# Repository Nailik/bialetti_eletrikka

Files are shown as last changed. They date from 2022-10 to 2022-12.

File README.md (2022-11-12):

# Bialetti Eletrikka

Modifiaction of the Bialetti Eletrikka in order to control the Heat by a Microcontroller with multiple TSiC Temperatur Sensors.

Currently the PCB is created and some sample/test software in development.

Preview of the PCB inside the Bottom of the Machine (the Bottom neeeds to be custom 3d printed).

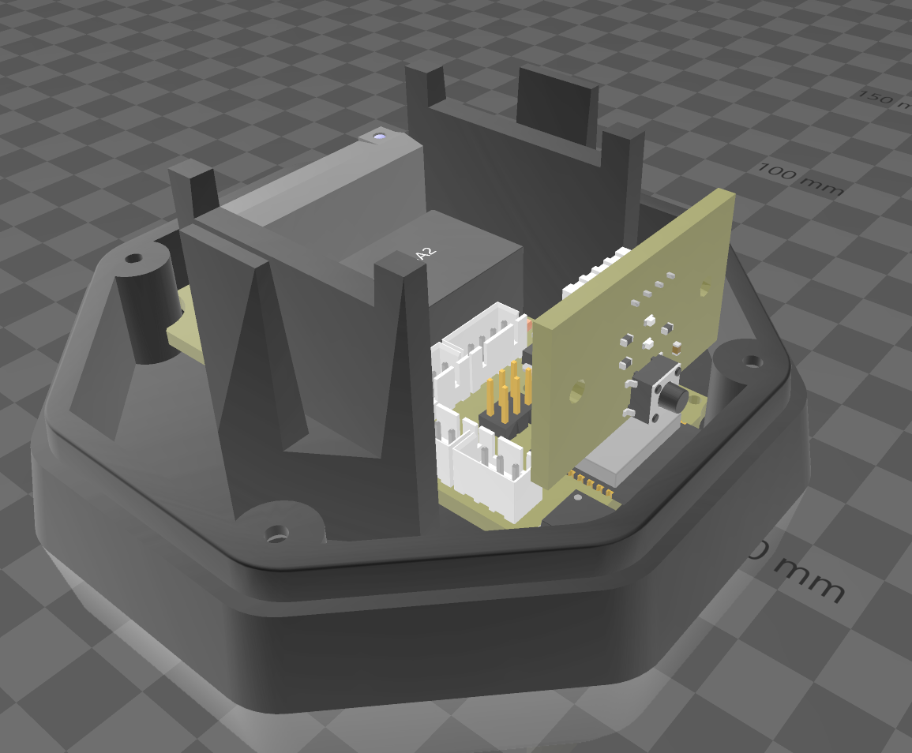
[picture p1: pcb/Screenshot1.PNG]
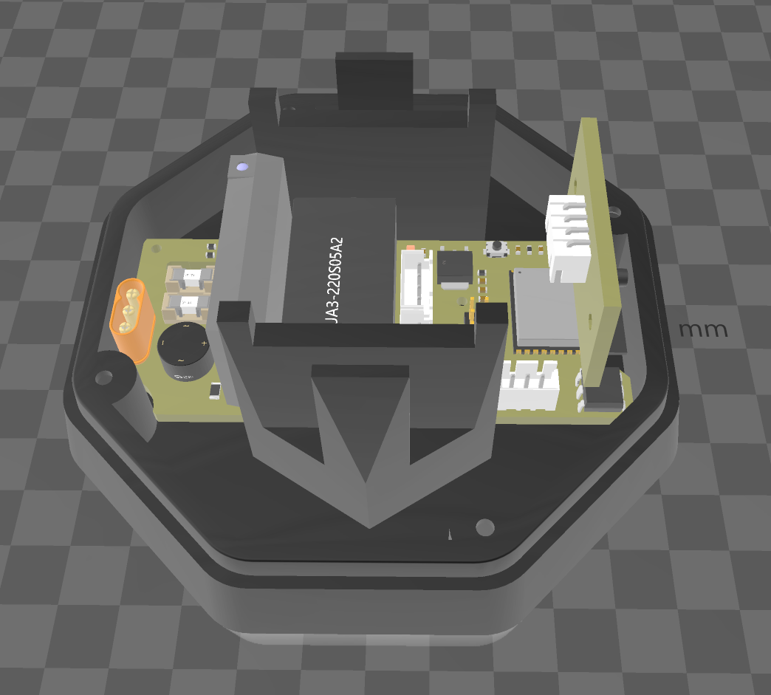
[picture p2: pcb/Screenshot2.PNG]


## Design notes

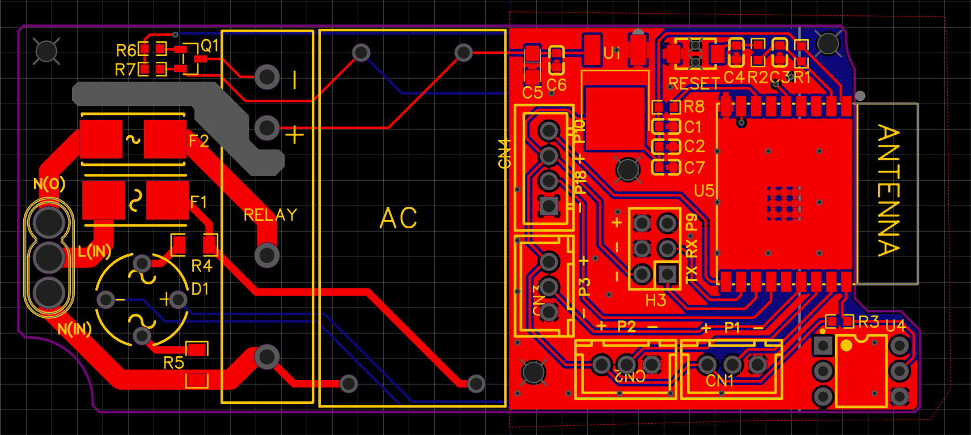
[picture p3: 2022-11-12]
pcb/Electric Mokka Pot-SSR/PCB.PNG

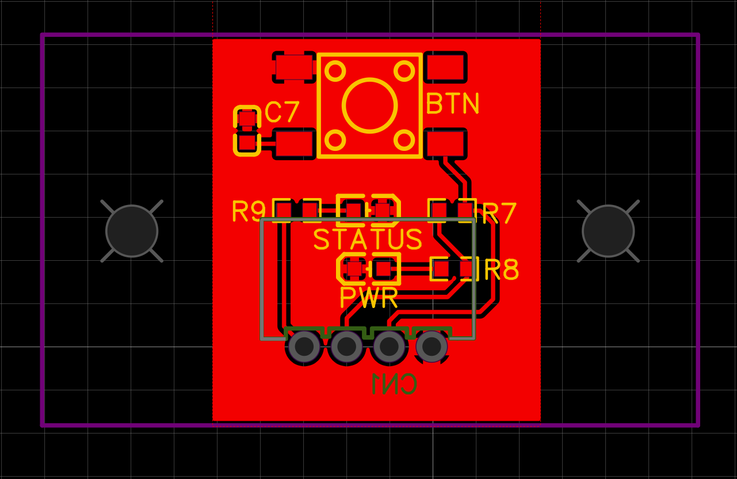
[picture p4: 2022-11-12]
pcb/Electric Mokka Pot - Button/PCB.PNG

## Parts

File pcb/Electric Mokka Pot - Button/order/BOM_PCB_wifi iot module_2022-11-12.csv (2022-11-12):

ID | Name | Designator | Footprint | Quantity | Manufacturer Part | Manufacturer | Supplier | Supplier Part | Price
1 | 0.1uf | C7 | C0603 | 1
2 | 10k | R7 | R0603 | 1
3 | UK-B0228-G5-160-JZ | BTN | KEY-SMD_4P-L6.0-W6.0-P4.50-LS11.0 | 1 | UK-B0228-G5-160-JZ | USAKRO | LCSC
4 | 68Ω | R8 | R0603 | 1
5 | 15Ω | R9 | R0603 | 1
6 | C2290 | PWR,STATUS | LED0603-R-RD_WHITE | 2 | 0603White light | KENTO | LCSC
7 | XH2.54-4AW | CN1 | CONN-TH_XH2.54-4AW | 1 | XH2.54-4AW | BOOMELE | LCSC

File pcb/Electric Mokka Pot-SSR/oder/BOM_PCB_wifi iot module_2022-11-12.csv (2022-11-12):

ID | Name | Designator | Footprint | Quantity | Manufacturer Part | Manufacturer | Supplier | Supplier Part | Price
1 | XH-4A | CN4 | CONN-TH_4P-P2.50_XH-4A | 1 | XH-4A | BOOMELE | LCSC
2 | XH-3A | CN1,CN2,CN3 | CONN-TH_XH-3A | 3 | XH-3A | BOOMELE | LCSC
3 | ESP32-C3-WROOM-02-N4(4MB) | U5 | BULETM-SMD_ESPRESSIF_ESP32-C3-WROOM-02-N4-4MB | 1 | ESP32-C3-WROOM-02-N4(4MB) | ESPRESSIF 乐鑫 | LCSC
4 | 10k | R8,R1,R3 | R0603 | 3
5 | PZ254V-12-6P | H3 | HDR-TH_6P-P2.54-V-M-R2-C3-S2.54 | 1 | PZ254V-12-6P | XFCN | LCSC
6 | 10uf | C1,C7 | C0603 | 2
7 | 0.1uf | C2,C4,C6 | C0603 | 3
8 | 1uf | C3 | C0603 | 1
9 | 0 | R2 | R0603 | 1
10 | 2K2 | R6 | R0603 | 1
11 | 10K | R7 | R0603 | 1
12 | 2N7002 | Q1 | SOT-23-3_L2.9-W1.3-P1.90-LS2.4-BR | 1 | 2N7002 | CJ | LCSC
13 | MR30-M | U2 | CONN-TH_MR30-M | 1 | MR30-M | AMASS(艾迈斯) | LCSC
14 | UA3-220S05A2 | PWR | PWRM-TH_UA3-220S05A2 | 1 | UA3-220S05A2 | Guangzhou Aipu Elec Tech | LCSC
15 | KSD203AC2 | RELAY | OPTO-TH_KSD203AC2 | 1 | KSD203AC2 | cosmo(冠西) | LCSC
16 | LD1117DT33TR | U1 | TO-252-2_L6.6-W6.1-P4.57-LS9.9-BR-CW | 1 | LD1117DT33TR | STMicroelectronics | LCSC
17 | 2W10M | D1 | DIO-BG-TH_WOB | 1 | 2W10M | Semtech | LCSC
18 | CT4N25 | U4 | DIP-6_L7.1-W6.5-P2.54-LS7.6-BL | 1 | CT4N25 | CT Micro International | LCSC
19 | TS-1088-AC02516 | RESET | SW-SMD_L4.0-W2.9-LS4.8 | 1 | TS-1088-AC02516 | XUNPU | LCSC
20 | 30kΩ | R4,R5 | R1206 | 2 | 1206W4F3002T5E | UNI-ROYAL(厚声) | LCSC
21 | 47uf | C5 | CASE-A_3216 | 1
22 | 0154002.DR | F1 | FUSE-SMD_L9.7-W5.0-1 | 1 | 0154002.DR | Littelfuse(美国力特) | LCSC
23 | 0154003.DR | F2 | FUSE-SMD_L9.7-W5.0 | 1 | 0154003.DR | Littelfuse | LCSC

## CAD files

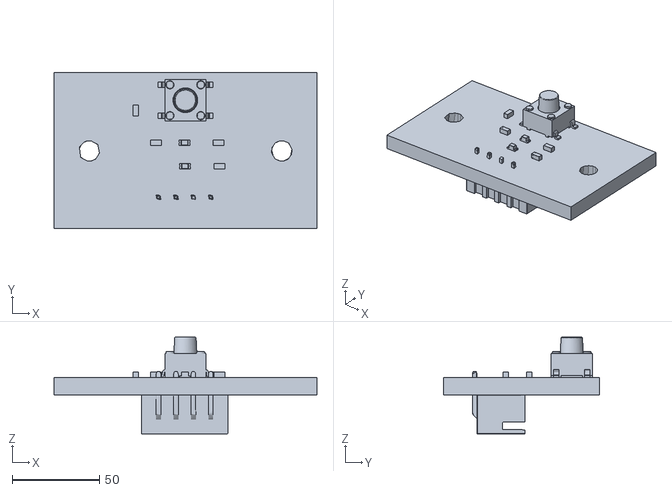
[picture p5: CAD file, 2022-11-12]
pcb/3d/Button/OBJ_PCB_wifi iot module.obj
150.8 x 89.3 x 55.5

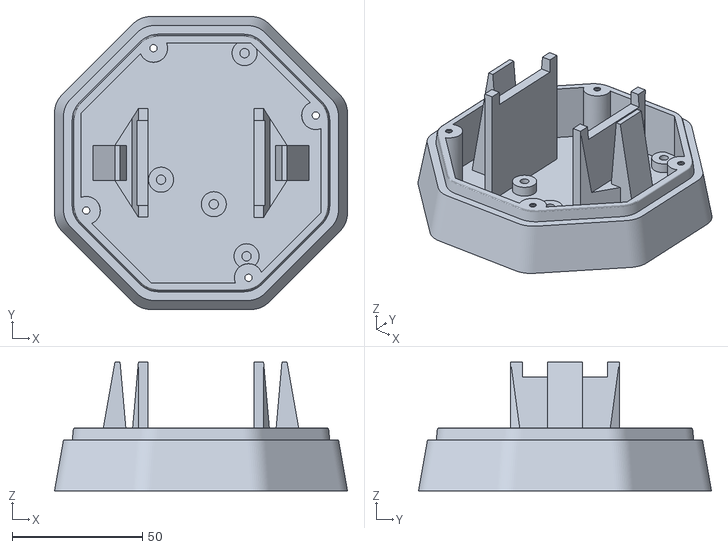
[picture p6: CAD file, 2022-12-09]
pcb/3d/Case.stl
112.3 x 112.3 x 49.3

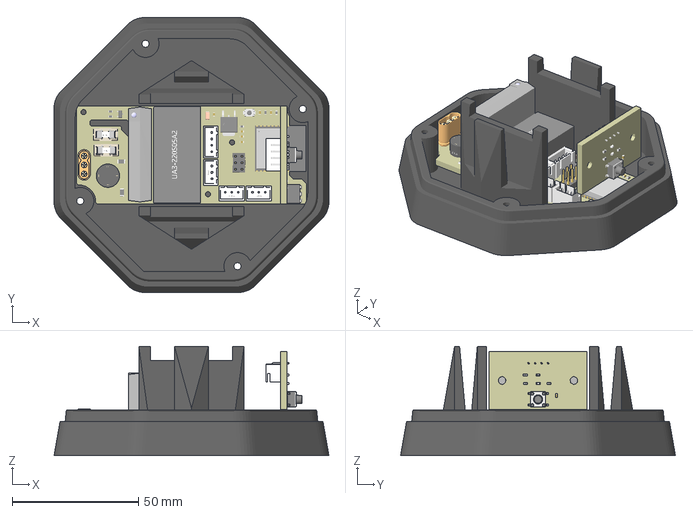
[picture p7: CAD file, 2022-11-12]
pcb/3d/fitcheck.3mf
108.8 x 108.8 x 43.3 mm

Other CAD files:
pcb/3d/mokka bottom v33.f3d

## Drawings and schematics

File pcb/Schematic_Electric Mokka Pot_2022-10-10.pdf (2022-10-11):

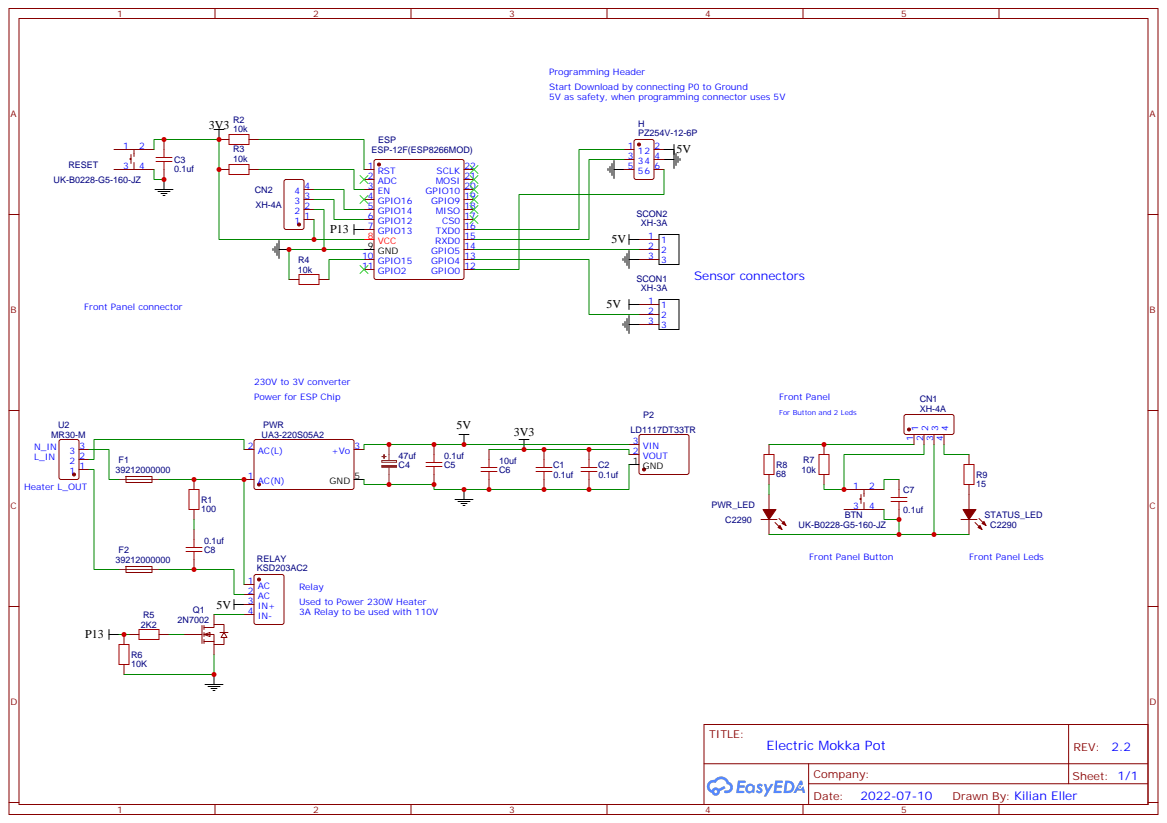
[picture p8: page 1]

Programming Header
Start Download by connecting P0 to Ground
5V as safety, when programming connector uses 5V

230V to 3V converter
Power for ESP Chip

For Button and 2 Leds

Relay
Used to Power 230W Heater
3A Relay to be used with 110V

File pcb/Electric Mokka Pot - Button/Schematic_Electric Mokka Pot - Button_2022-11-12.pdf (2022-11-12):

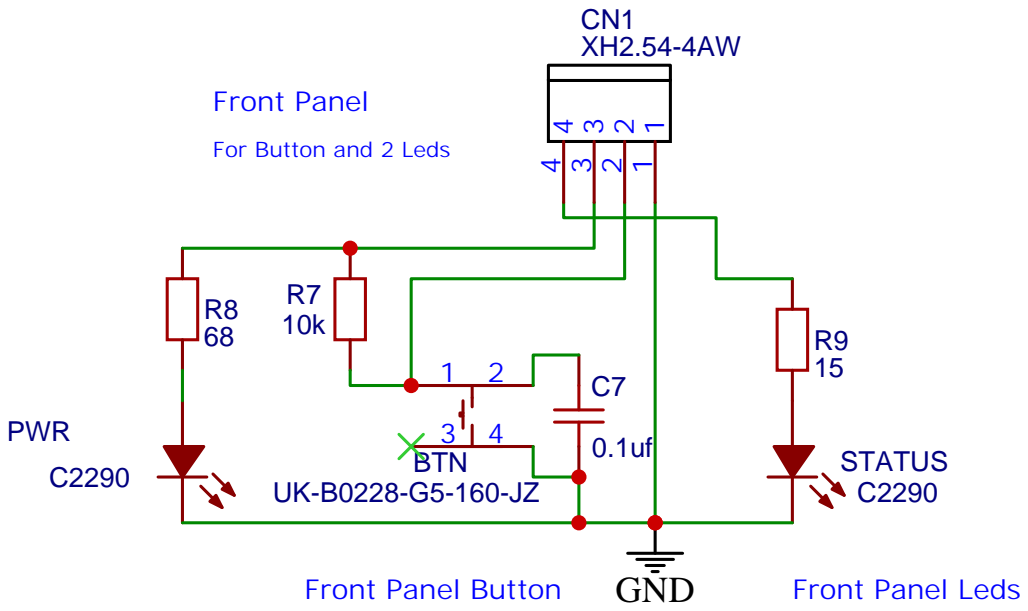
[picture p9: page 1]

For Button and 2 Leds

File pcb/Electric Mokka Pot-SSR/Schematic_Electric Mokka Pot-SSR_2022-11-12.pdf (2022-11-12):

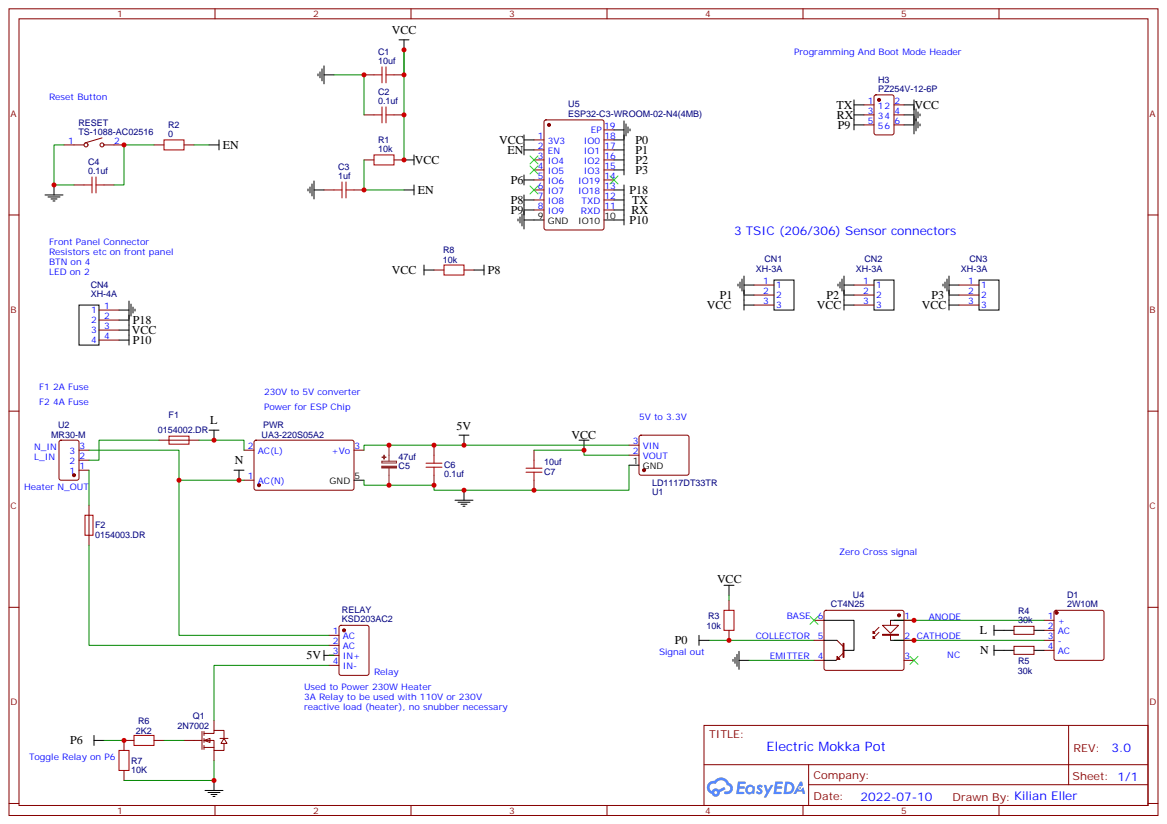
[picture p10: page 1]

Programming And Boot Mode Header

Front Panel Connector
Resistors etc on front panel
BTN on 4
LED on 2

Used to Power 230W Heater
3A Relay to be used with 110V or 230V
reactive load (heater), no snubber necessary

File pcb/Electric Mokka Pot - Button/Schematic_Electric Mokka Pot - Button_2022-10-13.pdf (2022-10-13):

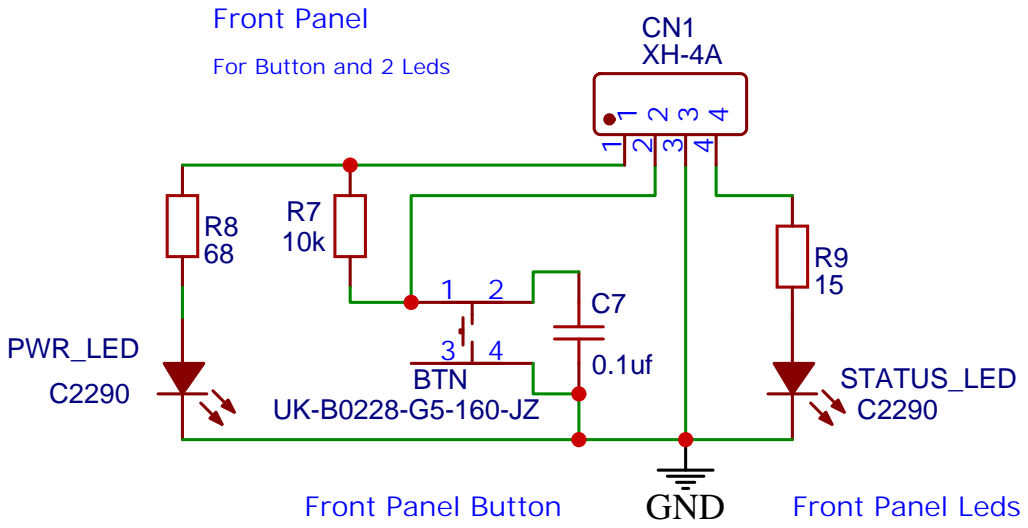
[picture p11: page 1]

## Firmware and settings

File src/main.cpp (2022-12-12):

#include <Arduino.h>
#include "webserver.h"
#include "sensors.h"
#include "actions.h"
#include "pid.h"
#include "WebSerialLite.h"

//https://github.com/Dlloydev/QuickPID
//https://github.com/Dlloydev/sTune
void setup() {
    Serial.begin(115200);
    Serial.println("startup");
    // put your setup code here, to run once:
    Sensors::setup();
    Serial.println("Sensors");
    Actions::setup();
    Serial.println("Actions");
    WebServer::setup();
    Serial.println("WebServer ");
    Pid::setup();
}

void loop() {
    // put your main code here, to run repeatedly:
    Sensors::loop();
    //custom loop for pid
    WebServer::loop();

    if (Serial.available()) {      // If anything comes in Serial (USB),
        WebSerial.println(Serial.readString());
    }

    delay(100);
}

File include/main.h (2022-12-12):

//
// Created by kilia on 12.08.2022.
//

#ifndef UNTITLED_MAIN_H
#define UNTITLED_MAIN_H

#define PIN_LED 10     //status led
#define PIN_BUTTON 18  //button
#define PIN_RELAY 6 //relay on/off
#define PIN_SENSOR_1 1 //TsiC 1
#define PIN_SENSOR_2 2 //TsiC 2
#define PIN_SENSOR_3 3 //TsiC 3 - connected initial
#define PIN_SIGNAL_ZC 0 //zero cross signal

#endif //UNTITLED_MAIN_H

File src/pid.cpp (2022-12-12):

/******************************************************************
  sTune QuickPID Example
  This sketch does on-the-fly tunning and PID Digital Output control
  of a thermal heater (TIP31C). Tunning parameters are quickly
  determined and applied during the temperature ramp-up to setpoint.
  Open the serial plotter to view the graphical results.

bei 65 grad kocht das wasser schon

 ----------------------------------------------
 testTimeSec = 50
 SetPoint = 40
 outputStep = 1

  .00
 Sampl:        0.1000

 Pv Start:          0.000
 Pv Max:            50.418
 Pv Diff:           50.418

 Process Gain:      252.092
 Dead Time Sec:     1.209
 Tau Sec:           87.079

 Tau/Dead Time:     72.0 (easy to control)
 Tau/Sample Period: 870.8 (good sample rate)

 Tuning Method: NoOvershoot_PID
  Kp: 0.171
  Ki: 0.011  Ti: 14.926
  Kd: 1.654  Td: 0.104


   ----------------------------------------------
 SetPoint = 65 (overshoot in beginning big, later up to 67,5°C)
 outputStep = 10
 directIP

  Ip Pv:             34.250
 Pv Start:          0.000
 Pv Max:            162.689
 Pv Diff:           162.689

 Process Gain:      271.148
 Dead Time Sec:     1.207
 Tau Sec:           1.880

 Tau/Dead Time:     1.6 (easy to control)
 Tau/Sample Period: 56.4 (good sample rate)

 Tuning Method: NoOvershoot_PID
  Kp: 0.003
  Ki: 0.532  Ti: 0.006
  Kd: 1.658  Td: 0.002





 ________________________________________





 Testen:


 Heizen -> Druckaufbau -> mehr Energie notwendig
 sobald Druck > Kaffee Druck -> Druck fällt -> weniger Energie notwendig
 Wasser neigt sich Ende -> deutlich weniger Energie -> zufuhr Abschalten, kein Sprudeln

 eigenes soft pwm
 tau (differenz zwischen windows messen bei x energie)
 0 - 100% energie





  *****************************************************************/

#include <cstdint>
#include "sensors.h"
#include "pid.h"
#include "main.h"
#include <Arduino.h>

float Pid::Output = 480;
float Pid::SetPoint = 98;
float Pid::FirstSetPoint = 80;
float Pid::Offset = 1;
float Pid::MaximumOutput = 480;
//window size in ms
uint32_t Pid::WindowSize = 480;
float Pid::TempLimit = 120;
int Pid::ZCTime = 0;
unsigned long Pid::ZCTimeLast = 0;
int Pid::value = 0;

void Pid::setup() {
    pinMode(PIN_RELAY, OUTPUT);
    digitalWrite(PIN_RELAY, LOW);

    attachInterrupt(digitalPinToInterrupt(PIN_SIGNAL_ZC), read, RISING);
}

//läuft alle 100 ms
void Pid::loop() {
    //Pid::zero_cross_int();
}

//output = ms zeit im fenster
float Pid::softPwm(float input, float output, float setpoint, uint32_t windowSize) {
//TODO every 8 ms
    static bool forceStop;
    static float inputChangeLastWindowStart;
    static float inputWindowStart;

    if (input >= TempLimit) {
        //blink led
        //forceStop = true;
    }

    if (forceStop) {
        //  digitalWrite(PIN_RELAY, LOW);
        //  return -1;
    }

    //current time
    uint32_t msNow = millis();

    static uint32_t windowStartTime;

    //seit begin dess windows ist alle zeit vergangen -> neues window hat gestartet
    if (msNow - windowStartTime >= windowSize) {
        windowStartTime = msNow;
        inputChangeLastWindowStart = input - inputWindowStart;
        inputWindowStart = input;
    }

    // SSR optimum AC half-cycle controller
    static float optimumOutput;
    static bool reachedFirstSetpoint;
    static bool reachedSetpoint;

    if (input >= FirstSetPoint) reachedFirstSetpoint = true;
    if (input >= SetPoint) reachedSetpoint = true;

    //degree to power percentage ratio 1:1
    if (!reachedFirstSetpoint) {
        //1:1
        optimumOutput = MaximumOutput;
    } else {
        //1:1
        optimumOutput = MaximumOutput * (1 - (input / SetPoint));
    }

    /*
    static bool reachedSetpoint;
    static bool reachedFirstSetpoint;

    if (input >= FirstSetPoint) reachedFirstSetpoint = true;

    //wurde setpoint erreicht?
    if (input >= setpoint) reachedSetpoint = true;

    if (reachedSetpoint && setpoint > 0 && input > setpoint) {
        //wurde setpoint schonmal erreicht und input immernoch größer als setpoint, dann output -8
        optimumOutput = output - 8;
    }
    else if (reachedSetpoint && setpoint > 0 && input < setpoint) {
    //wurde setpoint schonmal erreicht und input kleiner setpoint, dann output erhöhen
        optimumOutput = output + 8;
    }
    else if (reachedFirstSetpoint)  {
        //would setpoint be reached within overshoottime?
        if(input + (inputChangeLastWindowStart * (OvershootTime/WindowSize)) >= setpoint) {
            //decrease power
            optimumOutput = output - 8;
        } else {
            //increase power
            optimumOutput = output + 8;
        }
        //decrease power slowly if temp is rising
    }
    else {
        optimumOutput = output;
    }*/

    //optimum output = output, setpoint wurde noch nie erreicht
  //  if (optimumOutput < 0) optimumOutput = 0;

   // if (optimumOutput > MaximumOutput) optimumOutput = MaximumOutput;

    //optimale output größer als restzeit des fensters
  //  if (optimumOutput > (msNow - windowStartTime)) {

  //      digitalWrite(PIN_RELAY, HIGH);
 //   } else if (optimumOutput < (msNow - windowStartTime)) {

    //    digitalWrite(PIN_RELAY, LOW);
  //  }

    //return optimumOutput
    return optimumOutput;
}

void Pid::read() {
//    unsigned long current = micros();
 //   ZCTime = current - ZCTimeLast;
 //   ZCTimeLast = current;
    // Zündzeitpunkt berechnen : 1 full 50Hz wave =1/50=20ms
    // Jeder Nulldurchgang: (50Hz)-> 10ms (1/2 Cycle)
    // 10ms=10000us
    // (10 000us - 10us) / 100 = 99 (approx)
    //
    //max 0.3% = dimtime max = 2.997

   // ZCTime = dimtime;



    if (value == 0) {
        digitalWrite(PIN_RELAY, LOW);
    } else {
        int dimtime = 9900 - (25 * value); //dimTIme is minimum  7400us that's 85% therefore max output ist 25%
        if(dimtime < 7400){
            dimtime = 7400;
        }
        delayMicroseconds(dimtime);    // Wartet die Zeit zum zünden des TRIAC
        digitalWrite(PIN_RELAY, HIGH);   // zünde TRIAC
        delayMicroseconds(10);         // pause zum durchzünden
        digitalWrite(PIN_RELAY, LOW);    // TRIAC löschen
    }

}

void Pid::setPidPercentage(int percentage){
    if(percentage > 100 || percentage < 0){
        //check for valid value
        value = 0;
    } else {
        value = percentage;
    }
}

int Pid::getPidPercentage() {
    return value;
}

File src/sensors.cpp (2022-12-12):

//
// Created by kilia on 14.08.2022.
//

#include <Arduino.h>
#include "sensors.h"
#include "main.h"
#include "ZACwire.h"
#include "actions.h"
#include "pid.h"

int Sensors::button = 0;
int Sensors::relay = 0;
int Sensors::led = 0;
float Sensors::temp_1 = 0;
float Sensors::temp_2 = 0;
float Sensors::temp_3 = 0;

ZACwire Sensor1(PIN_SENSOR_1, 306);
ZACwire Sensor2(PIN_SENSOR_2, 306);
ZACwire Sensor3(PIN_SENSOR_3, 306);


void Sensors::setup() {
    Serial.println("Setup PIN_SENSOR_1");
    if (Sensor1.begin()) {     //check if a sensor is connected to the pin
        Serial.println("Signal found on pin PIN_SENSOR_1");
    }
    Serial.println("Setup PIN_SENSOR_2");
    if (Sensor2.begin()) {     //check if a sensor is connected to the pin
        Serial.println("Signal found on pin PIN_SENSOR_2");
    }
    Serial.println("Setup PIN_SENSOR_3");
    if (Sensor3.begin()) {     //check if a sensor is connected to the pin
        Serial.println("Signal found on pin PIN_SENSOR_3");
    }
    Serial.println("Setup PIN_BUTTON");
    attachInterrupt(PIN_BUTTON, isr_btn, CHANGE);
     ledcAttachPin(PIN_LED, 0);
    ledcSetup(0, 4000, 8);
}

void Sensors::loop() {
    //
    button = digitalRead(PIN_BUTTON);
    ledcWrite(0, uint8_t ((Pid::getPidPercentage()/100.0)*255.0));
    temp_1 = Sensor1.getTemp();
    temp_2 = Sensor2.getTemp();
    temp_3 = Sensor3.getTemp();
}

/**
 * called when button is pressed by isr
 *
 * @param button pointer to button that was pressed
 */
void IRAM_ATTR Sensors::isr_btn() {
    int state = digitalRead(PIN_BUTTON);
    Serial.println("isr_btn " + String(state));
    //will be high after button was released
    if (!state) {
        Actions::togglePid();
    }
}

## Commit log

2022-10-10 initial pcb
2022-10-11 simplified schematic
2022-10-13 split pcb into 2 projects removed snubber diode, as not necessary for reactive load
    [BOM_PCB_wifi iot module_2022-10-13.csv, PickAndPlace_PCB_wifi iot module_2022-10-13.csv]
2022-10-13 fixed button connector pins
    [BOM.csv, BOM_PCB_wifi iot module_2022-10-13.csv, PickAndPlace_PCB_wifi iot module_2022-10-13.csv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]
2022-11-12 added schematic
